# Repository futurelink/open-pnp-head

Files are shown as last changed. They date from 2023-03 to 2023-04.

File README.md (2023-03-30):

Versatile 4-nozzle PNP head controller
---

This controller was designed to be built into most of DIY pick-n-place machine heads.

### Features:
 - STM32F103C8T6 cheap MCU running on 72MHz
 - RS-485 control port
 - 4 rotary steppers running low-power STSPIN220 drivers
 - 2 up-down steppers running Pololu modules on your taste
 - 4 vacuum sensors to control part presence and place success
 - 4 isolated end-stop ports for home position identification
 - 4 isolated AO3400 MOSFET-driven ports to connect valves, solenoids etc.
 - head top light either WS2812 or LED-strip (5 or 12v)
 - Small size 80x65mm
 - No parts smaller than 0603 so can be hand-built.

### Board render:

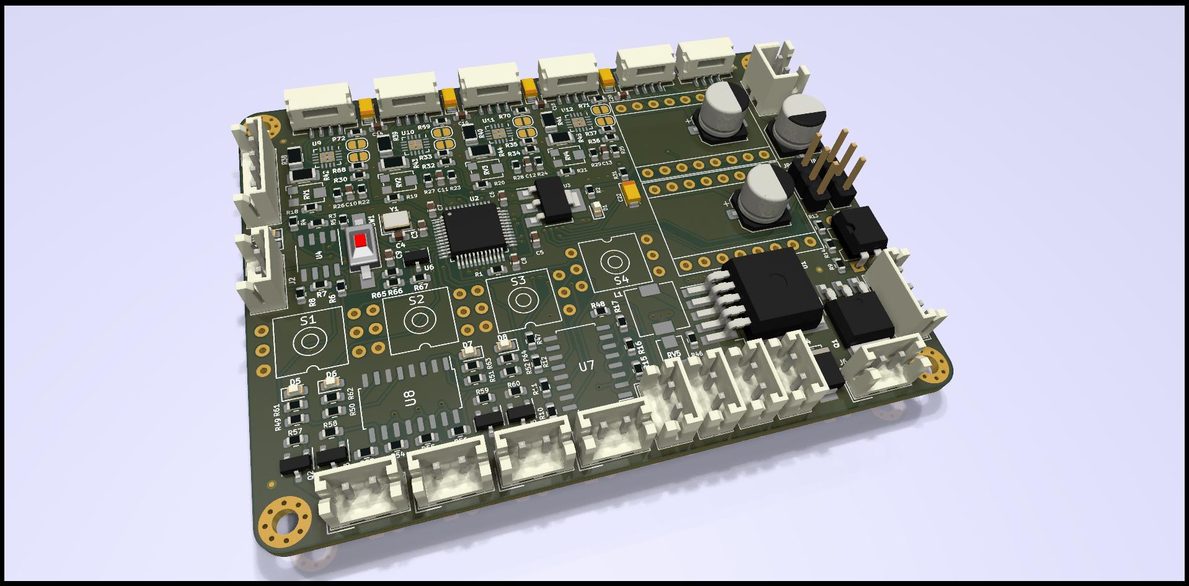
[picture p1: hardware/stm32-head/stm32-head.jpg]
render


### Disclaimer

This project is still in development, and it's not production ready.

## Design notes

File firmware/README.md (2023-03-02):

Modular CNC controller
---

This project is based on GRBL source code, deeply refactored, rewritten in C++
to make the code easier to understand and support.

Target platform to run this firmware is STM32F103C8T6, although it can be easily ported
to any other 32-bit MCU. Binary size with all available options switched on is about
76Kb.

### Supported hardware features

Mostly all features were derived from GRBL, some of them were added.

- Spindle (including PWM controlled)
- Coolant (Flood and Mist outputs)
- Limit switches (X, Y and Z)
- Probe
- Control inputs (Cycle start, Feed Hold, Reset and Safety door)
- Relay control 5 channels (turn on commands M100-M104, turn off - M110-M114)

### Running this firmware

Shortly - it can be run on a 'Blue Pill', USB is configured as Virtual COM port,
hence it's used to control and send G-Code. Typical speed is 115200.

Another option is to use controller designed for this firmware and it worth it because it has:

- opto-couplers in input and output lines (excluding control port and stepper drivers)
- RS-485 interface to control additional hardware
- 2 types of USB connectors (USB-B and JST embedding into one case with PC)
- 4 channels with MOSFETs to control relays (valves, solenoids) and separate (max. 24V) relay power input
- 1 channel with the same MOSFET but switchable power supply to connect work zone light
- spindle control 0-10V

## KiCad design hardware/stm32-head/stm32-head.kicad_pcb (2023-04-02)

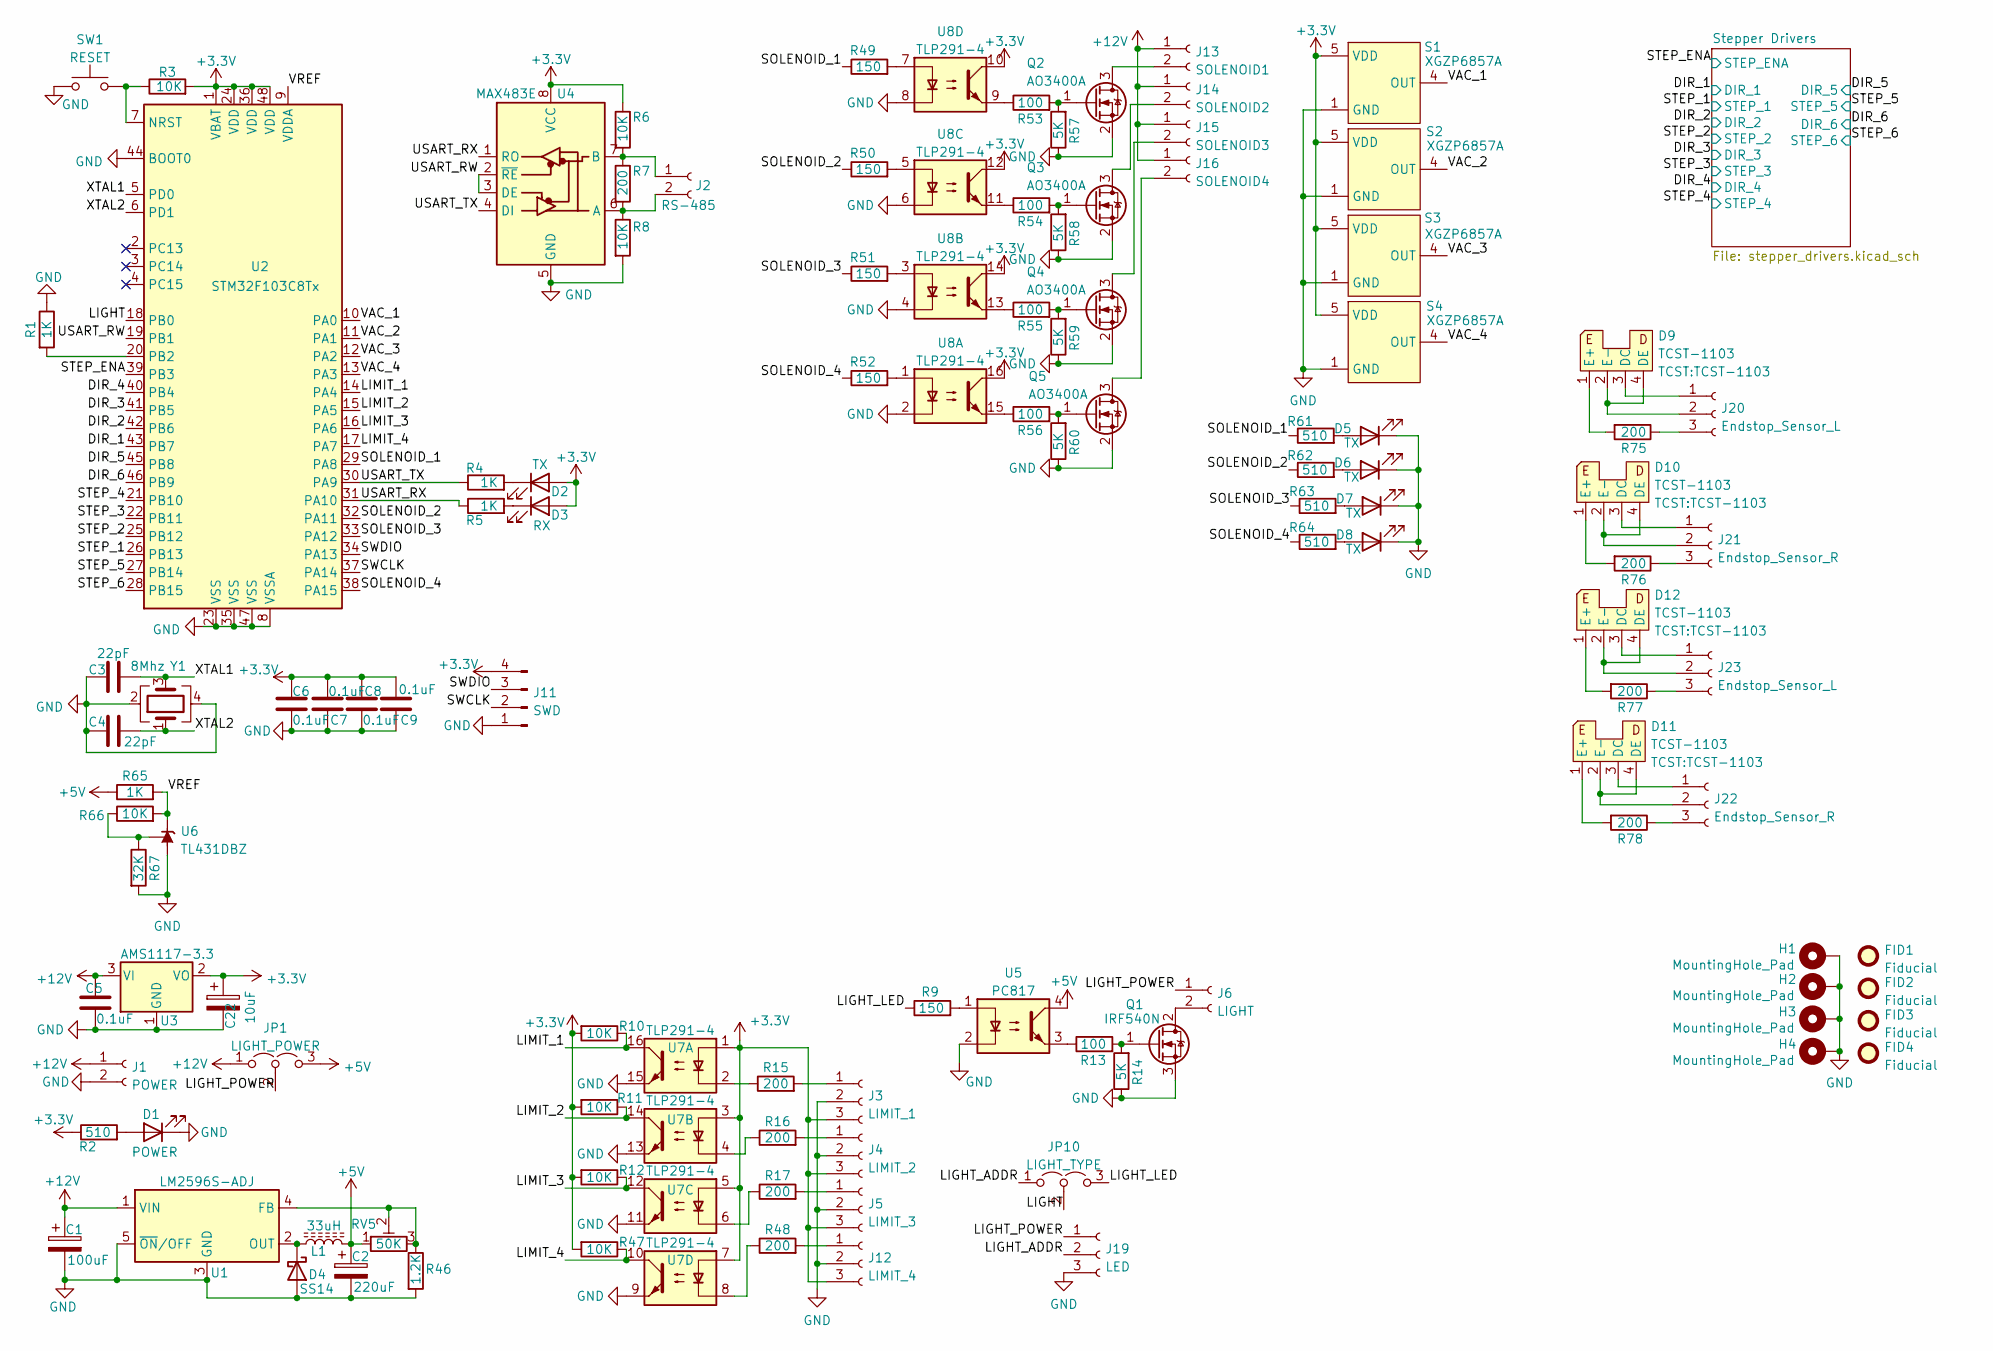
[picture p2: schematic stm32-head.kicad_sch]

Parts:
C1: 100uF; CP_Elec_6.3x5.9
C2: 220uF; CP_EIA-7343-31_Kemet-D
C3, C4: 22pF; C_0603_1608Metric
C5, C6, C7, C8, C9: 0.1uF; C_0603_1608Metric
C22: 10uF; CP_EIA-3216-12_Kemet-S
D1: POWER; LED_0603_1608Metric
D2, D5, D6, D7, D8: TX; LED_0603_1608Metric
D3: RX; LED_0603_1608Metric
D4: SS14; D_SMB
D9, D10, D11, D12: TCST-1103
FID1, FID2, FID3, FID4: Fiducial; Fiducial_0.5mm_Mask1mm
H1, H2, H3, H4: MountingHole_Pad; MountingHole_2.5mm_Pad_Via
J1: POWER; JST_XH_B2B-XH-A_1x02_P2.50mm_Vertical
J2: RS-485; JST_EH_B2B-EH-A_1x02_P2.50mm_Vertical
J3: LIMIT_1; JST_GH_BM03B-GHS-TBT_1x03-1MP_P1.25mm_Vertical
J4: LIMIT_2; JST_GH_BM03B-GHS-TBT_1x03-1MP_P1.25mm_Vertical
J5: LIMIT_3; JST_GH_BM03B-GHS-TBT_1x03-1MP_P1.25mm_Vertical
J6: LIGHT; JST_GH_BM02B-GHS-TBT_1x02-1MP_P1.25mm_Vertical
J11: SWD; JST_EH_B4B-EH-A_1x04_P2.50mm_Vertical
J12: LIMIT_4; JST_GH_BM03B-GHS-TBT_1x03-1MP_P1.25mm_Vertical
J13: SOLENOID1; JST_EH_B2B-EH-A_1x02_P2.50mm_Vertical
J14: SOLENOID2; JST_EH_B2B-EH-A_1x02_P2.50mm_Vertical
J15: SOLENOID3; JST_EH_B2B-EH-A_1x02_P2.50mm_Vertical
J16: SOLENOID4; JST_EH_B2B-EH-A_1x02_P2.50mm_Vertical
J19: LED; JST_EH_B3B-EH-A_1x03_P2.50mm_Vertical
J20, J23: Endstop_Sensor_L; JST_GH_SM03B-GHS-TB_1x03-1MP_P1.25mm_Horizontal
J21, J22: Endstop_Sensor_R; JST_GH_SM03B-GHS-TB_1x03-1MP_P1.25mm_Horizontal
JP1: LIGHT_POWER; PinHeader_1x03_P2.54mm_Vertical
JP10: LIGHT_TYPE; PinHeader_1x03_P2.54mm_Vertical
L1: 33uH; L_6.3x6.3_H3
Q1: IRF540N; TO-252-3_TabPin2
Q2, Q3, Q4, Q5: AO3400A; SOT-23
R1, R4, R5, R65: 1K; R_0603_1608Metric
R2, R61, R62, R63, R64: 510; R_0603_1608Metric
R3, R6, R8, R10, R11, R12, R47, R66: 10K; R_0603_1608Metric
R7, R15, R16, R17, R48, R75, R76, R77, R78: 200; R_0603_1608Metric
R9, R49, R50, R51, R52: 150; R_0603_1608Metric
R13, R53, R54, R55, R56: 100; R_0603_1608Metric
R14, R57, R58, R59, R60: 5K; R_0603_1608Metric
R46: 1.2K; R_0603_1608Metric
R67: 32K; R_0603_1608Metric
RV5: 50K; Potentiometer_Bourns_TC33X_Vertical
S1, S2, S3, S4: XGZP6857A; XGZP_Sensor_THT
SW1: RESET; SW_SPST_FSMSM
U1: LM2596S-ADJ; TO-263-5_TabPin3
U2: STM32F103C8Tx; LQFP-48_7x7mm_P0.5mm
U3: AMS1117-3.3; SOT-223-3_TabPin2
U4: MAX483E; SO-8_3.9x4.9mm_P1.27mm
U5: PC817; DIP-4_W7.62mm
U6: TL431DBZ; SOT-23
U7, U8: TLP291-4; SOIC-16_4.55x10.3mm_P1.27mm
Y1: 8Mhz; Crystal_SMD_3225-4Pin_3.2x2.5mm

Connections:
+3.3V: C6.2, C7.2, C8.2, C9.2, C22.1, D2.2 (A), D3.2 (A), J3.3, J4.3, J5.3, J11.4, J12.3, R2.1, R3.2, R6.1, R10.2, R11.2, R12.2, R47.2, S1.5 (VDD), S2.5 (VDD), S3.5 (VDD), S4.5 (VDD), U2.1 (VBAT), U2.24 (VDD), U2.36 (VDD), U2.48 (VDD), U3.2 (VO), U4.8 (VCC), U7.1, U7.3, U7.5, U7.7, U8.10, U8.12, U8.14, U8.16; also elsewhere on the board
+5V: C2.1, JP1.3 (B), L1.2, R65.1, RV5.1, U5.4; also elsewhere on the board
+12V: C1.1, C5.2, J1.1, J13.1, J14.1, J15.1, J16.1, JP1.1 (A), U1.1 (VIN), U3.3 (VI); also elsewhere on the board
/DIR_1: U2.43 (PB7); also elsewhere on the board
/DIR_2: U2.42 (PB6); also elsewhere on the board
/DIR_3: U2.41 (PB5); also elsewhere on the board
/DIR_4: U2.40 (PB4); also elsewhere on the board
/DIR_5: U2.45 (PB8); also elsewhere on the board
/DIR_6: U2.46 (PB9); also elsewhere on the board
/LIGHT: JP10.2 (C), U2.18 (PB0)
/LIGHT_ADDR: J19.2, JP10.1 (A)
/LIGHT_LED: JP10.3 (B), R9.1
/LIGHT_POWER: J6.1, J19.1, JP1.2 (C)
/LIMIT_1: R10.1, U2.14 (PA4), U7.16
/LIMIT_2: R11.1, U2.15 (PA5), U7.14
/LIMIT_3: R12.1, U2.16 (PA6), U7.12
/LIMIT_4: R47.1, U2.17 (PA7), U7.10
/SOLENOID_1: R49.1, R61.1, U2.29 (PA8)
/SOLENOID_2: R50.1, R62.1, U2.32 (PA11)
/SOLENOID_3: R51.1, R63.1, U2.33 (PA12)
/SOLENOID_4: R52.1, R64.1, U2.38 (PA15)
/STEP_1: U2.26 (PB13); also elsewhere on the board
/STEP_2: U2.25 (PB12); also elsewhere on the board
/STEP_3: U2.22 (PB11); also elsewhere on the board
/STEP_4: U2.21 (PB10); also elsewhere on the board
/STEP_5: U2.27 (PB14); also elsewhere on the board
/STEP_6: U2.28 (PB15); also elsewhere on the board
/STEP_ENA: U2.39 (PB3); also elsewhere on the board
/SWCLK: J11.2, U2.37 (PA14)
/SWDIO: J11.3, U2.34 (PA13)
/USART_RW: U2.19 (PB1), U4.2 (~RE), U4.3 (DE)
/USART_RX: R5.1, U2.31 (PA10), U4.1 (RO)
/USART_TX: R4.1, U2.30 (PA9), U4.4 (DI)
/VAC_1: S1.4 (OUT), U2.10 (PA0)
/VAC_2: S2.4 (OUT), U2.11 (PA1)
/VAC_3: S3.4 (OUT), U2.12 (PA2)
/VAC_4: S4.4 (OUT), U2.13 (PA3)
/VREF: R65.2, R66.2, U2.9 (VDDA), U6.1 (K)
/XTAL1: C3.2, U2.5 (PD0), Y1.3
/XTAL2: C4.2, U2.6 (PD1), Y1.1
GND: C1.2, C2.2, C3.1, C4.1, C5.1, C6.1, C7.1, C8.1, C9.1, C22.2, D1.1 (K), D4.2 (A), D5.1 (K), D6.1 (K), D7.1 (K), D8.1 (K), H1.1, H2.1, H3.1, H4.1, J1.2, J3.2, J4.2, J5.2, J11.1, J12.2, J19.3, Q1.3 (S), Q2.2 (S), Q3.2 (S), Q4.2 (S), Q5.2 (S), R1.1, R8.2, R14.1, R46.2, R57.1, R58.1, R59.1, R60.1, R67.2, S1.1 (GND), S2.1 (GND), S3.1 (GND), S4.1 (GND), SW1.1, U1.3 (GND), U1.5 (~ON/OFF), U2.8 (VSSA), U2.23 (VSS), U2.35 (VSS), U2.44 (BOOT0), U2.47 (VSS), U3.1 (GND), U4.5 (GND), U5.2, U6.3 (A), U7.9, U7.11, U7.13, U7.15, U8.2, U8.4, U8.6, U8.8, Y1.2, Y1.4; also elsewhere on the board
unnamed: D1.2 (A), R2.2
unnamed: D2.1 (K), R4.2
unnamed: D3.1 (K), R5.2
unnamed: D4.1 (K), L1.1, U1.2 (OUT)
unnamed: D5.2 (A), R61.2
unnamed: D6.2 (A), R62.2
unnamed: D7.2 (A), R63.2
unnamed: D8.2 (A), R64.2
unnamed: D9.1 (E+), R75.2
unnamed: D9.2 (E-), D9.4 (DE), J20.2
unnamed: D9.3 (DC), J20.1
unnamed: D10.1 (E+), R76.2
unnamed: D10.2 (E-), D10.4 (DE), J21.2
unnamed: D10.3 (DC), J21.1
unnamed: D11.1 (E+), R78.2
unnamed: D11.2 (E-), D11.4 (DE), J22.2
unnamed: D11.3 (DC), J22.1
unnamed: D12.1 (E+), R77.2
unnamed: D12.2 (E-), D12.4 (DE), J23.2
unnamed: D12.3 (DC), J23.1
unnamed: J2.1, R6.2, R7.1, U4.7 (B)
unnamed: J2.2, R7.2, R8.1, U4.6 (A)
unnamed: J3.1, R15.2
unnamed: J4.1, R16.2
unnamed: J5.1, R17.2
unnamed: J6.2, Q1.2 (D)
unnamed: J12.1, R48.2
unnamed: J13.2, Q2.3 (D)
unnamed: J14.2, Q3.3 (D)
unnamed: J15.2, Q4.3 (D)
unnamed: J16.2, Q5.3 (D)
unnamed: J20.3, R75.1
unnamed: J21.3, R76.1
unnamed: J22.3, R78.1
unnamed: J23.3, R77.1
unnamed: Q1.1 (G), R13.2, R14.2
unnamed: Q2.1 (G), R53.2, R57.2
unnamed: Q3.1 (G), R54.2, R58.2
unnamed: Q4.1 (G), R55.2, R59.2
unnamed: Q5.1 (G), R56.2, R60.2
unnamed: R1.2, U2.20 (PB2)
unnamed: R3.1, SW1.2, U2.7 (NRST)
unnamed: R9.2, U5.1
unnamed: R13.1, U5.3
unnamed: R15.1, U7.2
unnamed: R16.1, U7.4
unnamed: R17.1, U7.6
unnamed: R46.1, RV5.2, RV5.3, U1.4 (FB)
unnamed: R48.1, U7.8
unnamed: R49.2, U8.7
unnamed: R50.2, U8.5
unnamed: R51.2, U8.3
unnamed: R52.2, U8.1
unnamed: R53.1, U8.9
unnamed: R54.1, U8.11
unnamed: R55.1, U8.13
unnamed: R56.1, U8.15
unnamed: R66.1, R67.1, U6.2 (REF)

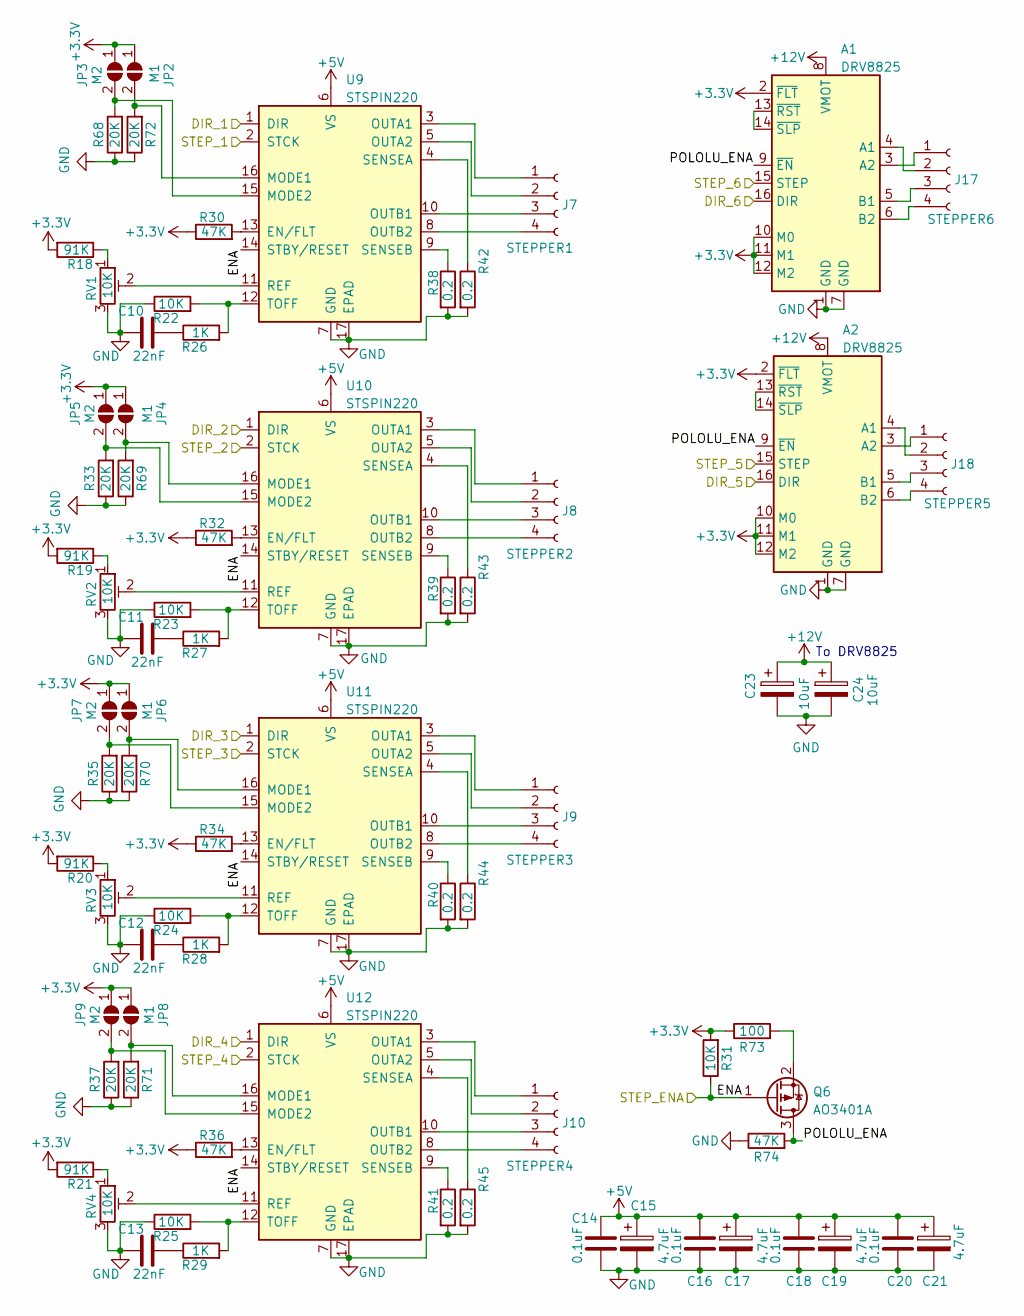
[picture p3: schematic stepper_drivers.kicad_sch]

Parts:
A1, A2: DRV8825; Pololu_Breakout-16_15.2x20.3mm
C10, C11, C12, C13: 22nF; C_0603_1608Metric
C14, C16, C18, C20: 0.1uF; C_0603_1608Metric
C15, C17, C19, C21: 4.7uF; CP_EIA-3216-10_Kemet-I
C23, C24: 10uF; CP_Elec_6.3x5.9
J7: STEPPER1; JST_GH_SM04B-GHS-TB_1x04-1MP_P1.25mm_Horizontal
J8: STEPPER2; JST_GH_SM04B-GHS-TB_1x04-1MP_P1.25mm_Horizontal
J9: STEPPER3; JST_GH_SM04B-GHS-TB_1x04-1MP_P1.25mm_Horizontal
J10: STEPPER4; JST_GH_SM04B-GHS-TB_1x04-1MP_P1.25mm_Horizontal
J17: STEPPER6; JST_GH_SM04B-GHS-TB_1x04-1MP_P1.25mm_Horizontal
J18: STEPPER5; JST_GH_SM04B-GHS-TB_1x04-1MP_P1.25mm_Horizontal
JP2, JP4, JP6, JP8: M1; SolderJumper-2_P1.3mm_Open_RoundedPad1.0x1.5mm
JP3, JP5, JP7, JP9: M2; SolderJumper-2_P1.3mm_Open_RoundedPad1.0x1.5mm
Q6: AO3401A; SOT-23
R18, R19, R20, R21: 91K; R_0603_1608Metric
R22, R23, R24, R25, R31: 10K; R_0603_1608Metric
R26, R27, R28, R29: 1K; R_0603_1608Metric
R30, R32, R34, R36, R74: 47K; R_0603_1608Metric
R33, R35, R37, R68, R69, R70, R71, R72: 20K; R_0603_1608Metric
R38, R39, R40, R41, R42, R43, R44, R45: 0.2; R_1206_3216Metric
R73: 100; R_0603_1608Metric
RV1, RV2, RV3, RV4: 10K; Potentiometer_Bourns_TC33X_Vertical
U9, U10, U11, U12: STSPIN220; VQFN-16-1EP_3x3mm_P0.5mm_EP1.8x1.8mm

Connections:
+3.3V: A1.2 (~FLT), A1.10 (M0), A1.11 (M1), A1.12 (M2), A2.2 (~FLT), A2.10 (M0), A2.11 (M1), A2.12 (M2), JP2.1 (A), JP3.1 (A), JP4.1 (A), JP5.1 (A), JP6.1 (A), JP7.1 (A), JP8.1 (A), JP9.1 (A), R18.2, R19.2, R20.2, R21.2, R30.1, R31.2, R32.1, R34.1, R36.1, R73.1; also elsewhere on the board
+5V: C14.1, C15.1, C16.1, C17.1, C18.1, C19.1, C20.1, C21.1, U9.6 (VS), U10.6 (VS), U11.6 (VS), U12.6 (VS); also elsewhere on the board
+12V: A1.8 (VMOT), A2.8 (VMOT), C23.1, C24.1; also elsewhere on the board
/DIR_1: U9.1 (DIR); also elsewhere on the board
/DIR_2: U10.1 (DIR); also elsewhere on the board
/DIR_3: U11.1 (DIR); also elsewhere on the board
/DIR_4: U12.1 (DIR); also elsewhere on the board
/DIR_5: A2.16 (DIR); also elsewhere on the board
/DIR_6: A1.16 (DIR); also elsewhere on the board
/STEP_1: U9.2 (STCK); also elsewhere on the board
/STEP_2: U10.2 (STCK); also elsewhere on the board
/STEP_3: U11.2 (STCK); also elsewhere on the board
/STEP_4: U12.2 (STCK); also elsewhere on the board
/STEP_5: A2.15 (STEP); also elsewhere on the board
/STEP_6: A1.15 (STEP); also elsewhere on the board
/STEP_ENA: Q6.1 (G), R31.1, U9.14 (STBY/RESET), U10.14 (STBY/RESET), U11.14 (STBY/RESET), U12.14 (STBY/RESET); also elsewhere on the board
/Stepper Drivers/POLOLU_ENA: A1.9 (~EN), A2.9 (~EN), Q6.3 (D), R74.2
GND: A1.1 (GND), A1.7 (GND), A2.1 (GND), A2.7 (GND), C10.1, C11.1, C12.1, C13.1, C14.2, C15.2, C16.2, C17.2, C18.2, C19.2, C20.2, C21.2, C23.2, C24.2, R22.1, R23.1, R24.1, R25.1, R33.1, R35.1, R37.1, R38.2, R39.2, R40.2, R41.2, R42.2, R43.2, R44.2, R45.2, R68.1, R69.1, R70.1, R71.1, R72.1, R74.1, RV1.3, RV2.3, RV3.3, RV4.3, U9.7 (GND), U9.17 (EPAD), U10.7 (GND), U10.17 (EPAD), U11.7 (GND), U11.17 (EPAD), U12.7 (GND), U12.17 (EPAD); also elsewhere on the board
unnamed: A1.3 (A2), J17.1
unnamed: A1.4 (A1), J17.2
unnamed: A1.5 (B1), J17.3
unnamed: A1.6 (B2), J17.4
unnamed: A1.13 (~RST), A1.14 (~SLP)
unnamed: A2.3 (A2), J18.1
unnamed: A2.4 (A1), J18.2
unnamed: A2.5 (B1), J18.3
unnamed: A2.6 (B2), J18.4
unnamed: A2.13 (~RST), A2.14 (~SLP)
unnamed: C10.2, R26.1
unnamed: C11.2, R27.1
unnamed: C12.2, R28.1
unnamed: C13.2, R29.1
unnamed: J7.1, U9.3 (OUTA1)
unnamed: J7.2, U9.5 (OUTA2)
unnamed: J7.3, U9.10 (OUTB1)
unnamed: J7.4, U9.8 (OUTB2)
unnamed: J8.1, U10.3 (OUTA1)
unnamed: J8.2, U10.5 (OUTA2)
unnamed: J8.3, U10.10 (OUTB1)
unnamed: J8.4, U10.8 (OUTB2)
unnamed: J9.1, U11.3 (OUTA1)
unnamed: J9.2, U11.5 (OUTA2)
unnamed: J9.3, U11.10 (OUTB1)
unnamed: J9.4, U11.8 (OUTB2)
unnamed: J10.1, U12.3 (OUTA1)
unnamed: J10.2, U12.5 (OUTA2)
unnamed: J10.3, U12.10 (OUTB1)
unnamed: J10.4, U12.8 (OUTB2)
unnamed: JP2.2 (B), R72.2, U9.16 (MODE1)
unnamed: JP3.2 (B), R68.2, U9.15 (MODE2)
unnamed: JP4.2 (B), R69.2, U10.16 (MODE1)
unnamed: JP5.2 (B), R33.2, U10.15 (MODE2)
unnamed: JP6.2 (B), R70.2, U11.16 (MODE1)
unnamed: JP7.2 (B), R35.2, U11.15 (MODE2)
unnamed: JP8.2 (B), R71.2, U12.16 (MODE1)
unnamed: JP9.2 (B), R37.2, U12.15 (MODE2)
unnamed: Q6.2 (S), R73.2
unnamed: R18.1, RV1.1
unnamed: R19.1, RV2.1
unnamed: R20.1, RV3.1
unnamed: R21.1, RV4.1
unnamed: R22.2, R26.2, U9.12 (TOFF)
unnamed: R23.2, R27.2, U10.12 (TOFF)
unnamed: R24.2, R28.2, U11.12 (TOFF)
unnamed: R25.2, R29.2, U12.12 (TOFF)
unnamed: R30.2, U9.13 (EN/FLT)
unnamed: R32.2, U10.13 (EN/FLT)
unnamed: R34.2, U11.13 (EN/FLT)
unnamed: R36.2, U12.13 (EN/FLT)
unnamed: R38.1, U9.9 (SENSEB)
unnamed: R39.1, U10.9 (SENSEB)
unnamed: R40.1, U11.9 (SENSEB)
unnamed: R41.1, U12.9 (SENSEB)
unnamed: R42.1, U9.4 (SENSEA)
unnamed: R43.1, U10.4 (SENSEA)
unnamed: R44.1, U11.4 (SENSEA)
unnamed: R45.1, U12.4 (SENSEA)
unnamed: RV1.2, U9.11 (REF)
unnamed: RV2.2, U10.11 (REF)
unnamed: RV3.2, U11.11 (REF)
unnamed: RV4.2, U12.11 (REF)

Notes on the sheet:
To DRV8825

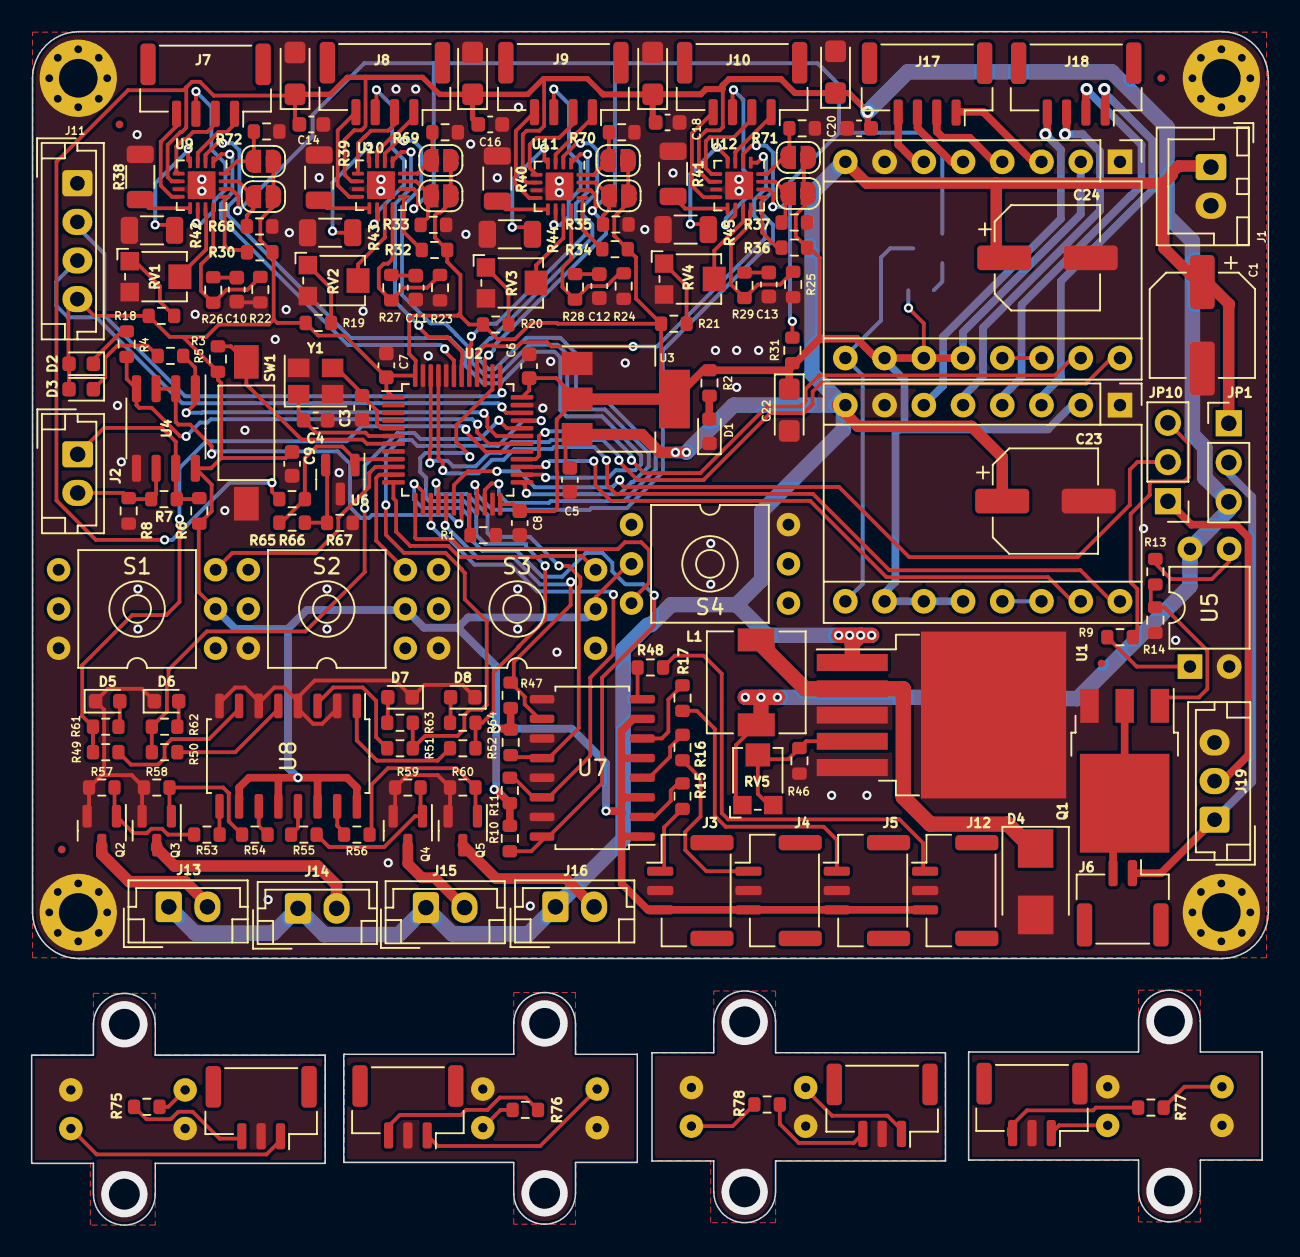
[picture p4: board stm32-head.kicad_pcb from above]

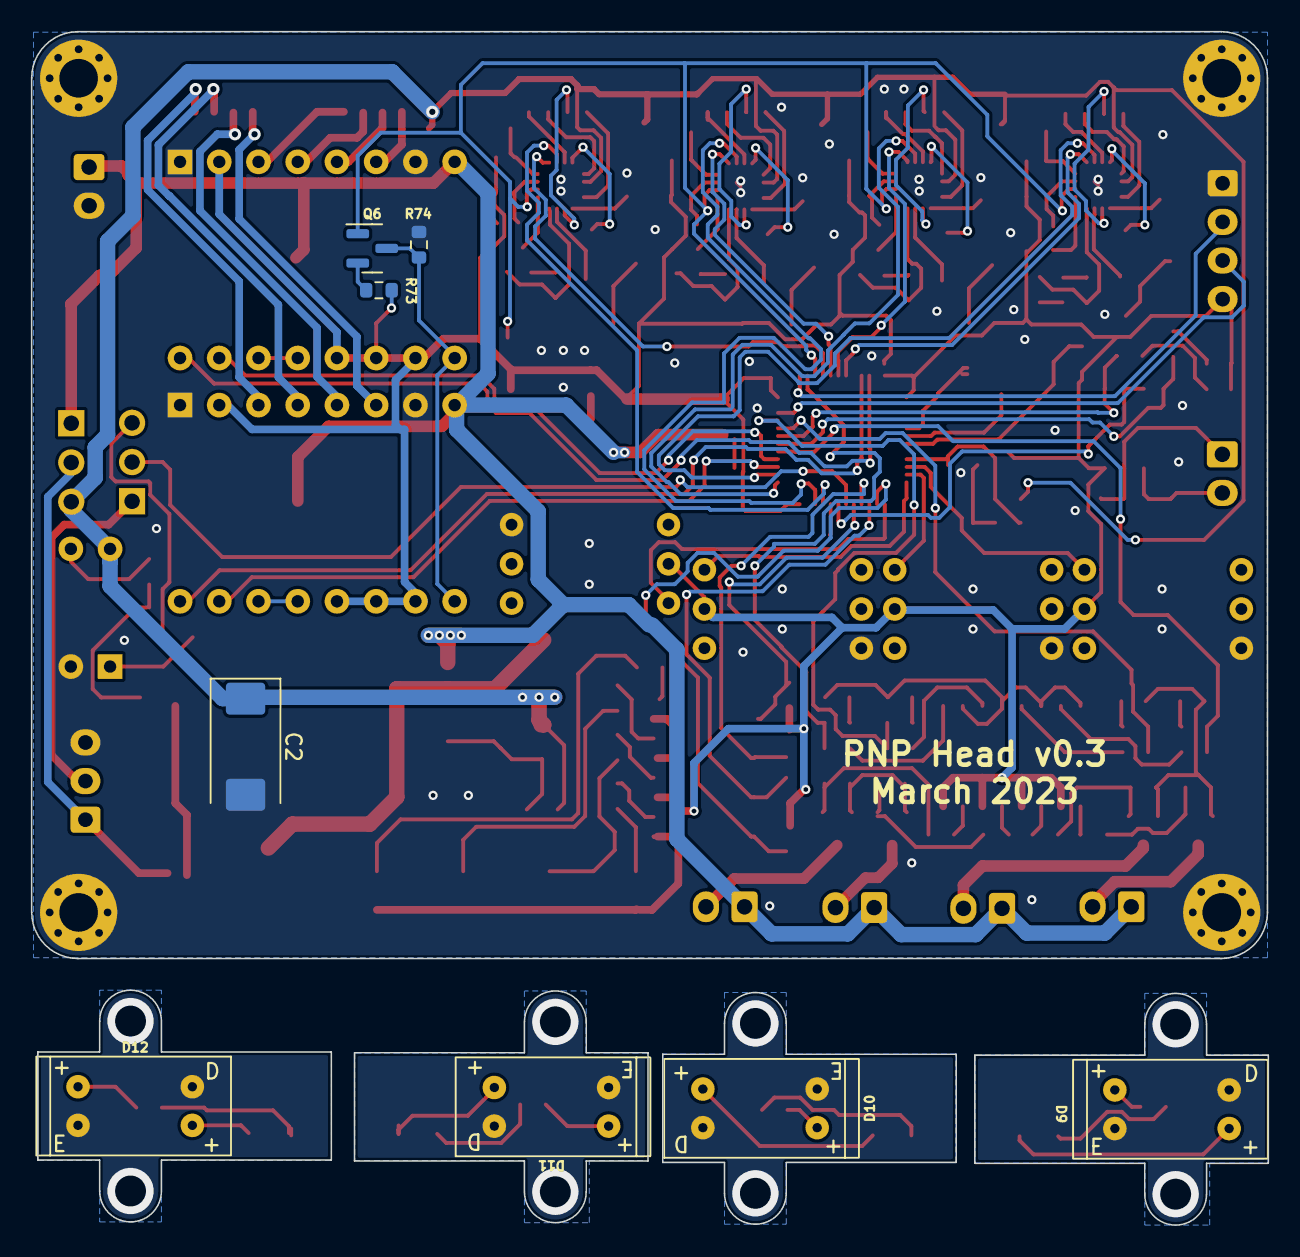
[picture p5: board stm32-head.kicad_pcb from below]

Board: 2 copper layers, 80.0 x 60.0 mm, 187 parts (8 on the bottom side), 163 nets.

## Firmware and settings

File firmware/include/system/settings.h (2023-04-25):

/*
  settings.h
  Part of open-pnp-head

  Copyright (c) 2022 Denis Pavlov

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
  You should have received a copy of the GNU General Public License
  along with open-pnp-head.  If not, see <http://www.gnu.org/licenses/>.
*/

#ifndef SETTINGS_H
#define SETTINGS_H

#include "config.h"

#include <cstdint>

#define SETTINGS_VERSION 1

class Settings {
private:
    float       steps_per_degree;

    // Linear belt-driven head settings
    uint16_t    steps_per_mm;

#ifdef ROCKER_HEAD
    // Rocker-head settings
    float       arm_length;
    float       arm_center_offset;
    float       arm_roller_radius;

    // Internal variables
    float       arm_max_travel;
    float       arm_segment_length;
    float       step_increment[STEP_APPROX_SEGMENTS_N];
#endif

public:
    Settings();

    bool load();

    float get_steps_per_degree(uint8_t axis) const;
    uint16_t get_steps_per_mm(uint8_t axis) const;

    float get_acceleration(uint8_t axis) const;
    float get_speed(uint8_t axis) const;

    void convert_rotary_steps_to_degrees(float *position, const int32_t *steps, uint8_t n_axis) const;
    void convert_linear_steps_to_mm(float *position, const int32_t *steps, uint8_t n_axis) const;
    float convert_linear_steps_to_mm(int32_t steps) const;

    float get_linear_max_travel();

#ifdef ROCKER_HEAD
    void prepare_rocker_head_curve();
    float get_rocker_axis_position(int32_t position_steps) const;
    float get_rocker_axis_steps(float position, float destination) const;
#endif


};

inline float Settings::get_steps_per_degree(uint8_t axis) const { return steps_per_degree; }
inline uint16_t Settings::get_steps_per_mm(uint8_t axis) const { return steps_per_mm; }

#endif //SETTINGS_H

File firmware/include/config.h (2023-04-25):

/*
  config.h - main configuration
  Part of open-pnp-head

  Copyright (c) 2022 Denis Pavlov

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
  You should have received a copy of the GNU General Public License
  along with open-pnp-head.  If not, see <http://www.gnu.org/licenses/>.
*/

#include <cstdint>

#ifndef CONFIG_H
#define CONFIG_H

// Enables ModBus mode
#define MODBUS

#define BAUD_RATE           115200

#define GREETING_STRING     "PNP Head / v0.1\n"
#define LINE_MAX_LENGTH     80

// Turns on rocker head mode.
// Comment out to switch to linear movement mode
// ---------------------------------------------
#define ROCKER_HEAD

#define ROTARY_AXIS_N       4                       // Number of rotary axes i.e. nozzles
#define LINEAR_AXIS_N       (ROTARY_AXIS_N / 2)     // Number of linear/rocker axes
#define AXIS_N              (ROTARY_AXIS_N + LINEAR_AXIS_N)

// Axis direction inverted
#define AXIS_DIR_INVERT  ((1 << 0) | (1 << 1) | (2 << 1) | (3 << 1)) // All rotary axes

// Axis speed/acceleration settings
// --------------------------------
#define ROTARY_AXIS_ACCEL       25000               // deg/s^2
#define ROTARY_AXIS_SPEED       2500                // deg/s
#define ROTARY_STEP_PER_DEGREE  (200.0 * 16 / 360)  // steps/deg, 1/16 micro-step

// Vacuum sensors settings and minimum values
// ------------------------------------------
#define VAC_SENSORS_N                   4
#define VAC_SENSOR_1_MIN_PRESSURE       (-100) // kPa
#define VAC_SENSOR_2_MIN_PRESSURE       (-100) // kPa
#define VAC_SENSOR_3_MIN_PRESSURE       (-100) // kPa
#define VAC_SENSOR_4_MIN_PRESSURE       (-100) // kPa

// Number of relay outputs
// -----------------------
#define RELAY_N                         4

// Vacuum values with components sucked to nozzle
// ----------------------------------------------
#define VAC_SENSOR_1_LOCKED_PRESSURE    (-0.01) // kPa
#define VAC_SENSOR_2_LOCKED_PRESSURE    (-5) // kPa
#define VAC_SENSOR_3_LOCKED_PRESSURE    (-5) // kPa
#define VAC_SENSOR_4_LOCKED_PRESSURE    (-5) // kPa

#define STEPPER_ENABLE_INVERT
#define ACCELERATION_TICKS_PER_SECOND   50
#define STEP_PULSE_MS                   2

// Time in milliseconds to wait while pressure normalizes before measuring
// -----------------------------------------------------------------------
#define PICK_WAIT_TIME                  100  // when picking
#define PLACE_WAIT_TIME                 150  // when placing

// Rocker head settings
// --------------------
#ifdef ROCKER_HEAD
#define LINEAR_AXIS_ACCEL               4000                // mm/s^2
#define LINEAR_AXIS_SPEED               4000                // mm/s
#define STEP_PER_ROTATION               12800
#define STEP_APPROX_SEGMENTS_N          20
#define ARM_LENGTH                      31    // mm
#define ARM_CENTER_OFFSET               7       // mm
#define ARM_ROLLER_RADIUS               5       // mm
#else
#define LINEAR_AXIS_ACCEL               4000                // mm/s^2
#define LINEAR_AXIS_SPEED               4000                // mm/s
#define LINEAR_AXIS_MAX_TRAVEL          50.0F               // mm
#define LINEAR_STEP_PER_MM              160.0F              // steps/mm
#endif

// Addressable LED light settings
// ------------------------------
#define WS8212LED                               // Turns on addressable LEDs support
#define WS8212LED_N                     16      // LEDs number

#endif // CONFIG_H

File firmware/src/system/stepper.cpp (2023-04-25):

/*
  stepper.cpp - step motor control routines
  Part of open-pnp-head

  Copyright (c) 2022 Denis Pavlov

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
  You should have received a copy of the GNU General Public License
  along with open-pnp-head.  If not, see <http://www.gnu.org/licenses/>.
*/

#include <cmath>
#include <cstring>

#include "config.h"
#include "system/stepper.h"
#include "system/macros.h"
#include "stm32/stm32_routines.h"

Steppers::Steppers(Settings *settings, State *state, Callbacks *callbacks) {
    this->settings = settings;
    this->state = state;
    this->callbacks = callbacks;
    this->step_port_invert_mask = 0xffff;
    this->dir_port_invert_mask = axis_to_port_direction_bits(AXIS_DIR_INVERT);

    // Initialize structs with zeroes
    memset(&profile, 0, sizeof(profile_prep_t));
    memset(&st, 0, sizeof(stepper_t));

    this->planned_block = nullptr;
    this->segment_buffer_tail = 0;
    this->segment_buffer_head = 0;
    this->segment_next_head = 1;
    this->busy = false;

    this->segment_dt = 0;
    this->units_remaining = 0;
}

void Steppers::init() {
    stm32_stepper_init();
    go_idle();
    stm32_steppers_set(dir_port_invert_mask, step_port_invert_mask);
}

void Steppers::pulse_start() {
    if (!stm32_steppers_pulse_start(busy, st.dir_out_bits, st.step_out_bits)) return;

    busy = true;

    // If there is no step segment, attempt to pop one from the stepper buffer
    if (st.exec_segment == nullptr) {
        if (segment_buffer_head != segment_buffer_tail) { // Anything in the buffer? If so, load and initialize next step segment.
            st.exec_segment = &segment_buffer[segment_buffer_tail]; // Initialize new step segment and load number of steps to execute

            // Initialize step segment timing per step and load number of steps to execute.
            stm32_steppers_set_timer(st.exec_segment->cycles_per_tick);
            st.step_count = st.exec_segment->n_step;

            // If the new segment starts a new planner block, initialize stepper variables and counters.
            // NOTE: When the segment data index changes, this indicates a new planner block.
            if (st.exec_block_index != st.exec_segment->st_block_index) {
                st.exec_block_index = st.exec_segment->st_block_index;
                st.exec_block = &st_block_buffer[st.exec_block_index];

                // Initialize Bresenham line and distance counters
                for (uint32_t &counter : st.counters) counter = st.exec_block->step_event_count >> 1;
            }

            st.dir_out_bits = st.exec_block->dir_port_bits ^ dir_port_invert_mask;

            // With AMASS enabled, adjust Bresenham axis increment counters according to AMASS level
            for (uint8_t idx = 0; idx < (uint8_t) AXIS_N; idx++) {
                st.steps[idx] = st.exec_block->steps[idx] >> st.exec_segment->amass_level;
            }
        } else {
            go_idle(); // Segment buffer empty. Shutdown.
            state->set_state(state->get_state() | STATE_CYCLE_STOP);  // Flag for cycle end, keep cycle flag
            return;
        }
    }

    st.step_out_bits = 0; // Reset step out bits.

    // Execute step displacement profile by Bresenham line algorithm
    // -------------------------------------------------------------
    for (uint8_t idx = 0; idx < (uint8_t) AXIS_N; idx++) {
        st.counters[idx] += st.steps[idx];
        if (st.counters[idx] > st.exec_block->step_event_count) {
            st.step_out_bits |= step_pin_mask[idx];
            st.counters[idx] -= st.exec_block->step_event_count;
            if ((st.dir_out_bits ^ dir_port_invert_mask) & direction_pin_mask[idx])
                state->decrement_position(idx);
            else
                state->increment_position(idx);
        }
    }

    st.step_count--; // Decrement step events count
    if (st.step_count == 0) {
        st.exec_segment = nullptr; // Segment is complete. Discard current segment and advance segment indexing.

        uint8_t segment_tail_next = segment_buffer_tail + 1;
        segment_buffer_tail = (segment_tail_next == SEGMENT_BUFFER_SIZE) ? 0 : segment_tail_next;
    }

    st.step_out_bits ^= step_port_invert_mask;  // Apply step port invert mask
    busy = false;
}

void Steppers::pulse_end() const {
    stm32_steppers_pulse_end(step_port_invert_mask);
}

/**
 * Stepper state initialization
 */
void Steppers::wake_up() {
    stm32_steppers_enable();

    // Initialize stepper output bits to ensure first ISR call does not step.
    st.step_out_bits = step_port_invert_mask;

    // Set step pulse time. Ad-hoc computation from oscilloscope. Uses two's complement.
    st.step_pulse_time = STEP_PULSE_MS * TICKS_PER_MICROSECOND;

    stm32_steppers_wake_up(st.step_pulse_time, st.exec_segment->cycles_per_tick);
}

/**
 * Stepper shutdown
 */
void Steppers::go_idle() {
    stm32_steppers_go_idle();

    busy = false;
}

/**
 * Called by realtime status reporting to fetch the current speed being executed. This value
 * however is not exactly the current speed, but the speed computed in the last step segment
 * in the segment buffer. It will always be behind by up to the number of segment blocks (-1)
 * divided by the ACCELERATION TICKS PER SECOND in seconds.
 */
float Steppers::get_realtime_rate() const {
    return state->has_state(STATE_CYCLE_PICK | STATE_CYCLE_PLACE | STATE_CYCLE_ROTATE) ?
        profile.current_speed : 0.0f;
}

/**
 * Prepares buffer for stepper execution.
 * This method should be called as often as possible. Generally - from the main loop.
 */
void Steppers::prepare_buffer() {
    if (state->is_end_motion()) return;
    while (segment_buffer_tail != segment_next_head) {           // Check if we need to fill the buffer.
        if (!prepare_block()) return;                            // Bail out if there's no block to execute
        prepare_profile();
        prepare_segment(); // Initialize new segment
        if (check_end_motion()) {
            state->set_end_motion();
            return;
        }
    }
}
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

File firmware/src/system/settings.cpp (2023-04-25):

/*
  settings.cpp - settings management routines
  Part of open-pnp-head

  Copyright (c) 2022 Denis Pavlov

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
  You should have received a copy of the GNU General Public License
  along with open-pnp-head.  If not, see <http://www.gnu.org/licenses/>.
*/

#include "system/settings.h"

#include <cmath>

Settings::Settings() {

}

bool Settings::load() {
    steps_per_degree = ROTARY_STEP_PER_DEGREE; // 1/16 micro-stepping

#ifdef ROCKER_HEAD
    prepare_rocker_head_curve();
#else
    steps_per_mm = LINEAR_STEP_PER_MM;
#endif

    return true;
}

#ifdef ROCKER_HEAD
void Settings::prepare_rocker_head_curve() {
    arm_length = ARM_LENGTH;
    arm_center_offset = ARM_CENTER_OFFSET;
    arm_roller_radius = ARM_ROLLER_RADIUS;

    // Pre-calculate rocker-head curve approximation segments
    // ------------------------------------------------------
    auto steps_per_quarter = STEP_PER_ROTATION / 4;
    float degrees_per_step = 90.0f / (float) steps_per_quarter;
    arm_max_travel = arm_length - arm_center_offset + arm_roller_radius;
    arm_segment_length = arm_max_travel / STEP_APPROX_SEGMENTS_N;

    uint8_t segment = 0;
    uint16_t tmp_step_count = 0;
    float tmp_sum = 0;
    auto step = 0;
    auto step_radian = (float)(M_PI / 180 * degrees_per_step);
    while (step <= steps_per_quarter) {
        step++;
        tmp_sum += (sinf(step_radian * (float) step) - ((step == 0) ? 0.0f : sinf(step_radian * (float) (step - 1)))) * arm_max_travel;

        if ((tmp_sum >= arm_segment_length) || (step == steps_per_quarter)) {
            step_increment[segment] = arm_segment_length / (float) tmp_step_count;
            tmp_step_count = 0;
            tmp_sum -= (float) arm_segment_length;
            segment++;
        }
        tmp_step_count++;
    }
}

float Settings::get_rocker_axis_position(const int32_t position_steps) const {
    float position = 0;
    uint32_t abs_position_steps = abs(position_steps);

    // Calculate first incomplete segment steps
    // ...

    // Calculate full segments
    float steps = 0;
    uint8_t segment = 0;
    for (; segment < STEP_APPROX_SEGMENTS_N; segment++) {
        auto st_inc = arm_segment_length / step_increment[segment];
        if (steps + st_inc >= (float) abs_position_steps) break;
        position += arm_segment_length;
        steps += st_inc;
    }

    // Calculate remainder
    auto remain_steps = (float) abs_position_steps - steps;
    if (remain_steps > 0) position += remain_steps * step_increment[segment];

    return position * ((position_steps < 0) ? -1.0f : 1.0f);
}

float Settings::get_rocker_axis_steps(const float position, const float destination) const {
    if (position == destination) return 0;

    auto abs_position = fabsf(position);
    auto abs_destination = fabsf(destination);
    float steps = 0;

    // The main idea of this algorithm is to place finalizing segment at the end, so whatever
    // movement is being done the incomplete segment will always be the final thing to be processed.
    uint8_t dir = abs_position < abs_destination ? 0 : 1;
    auto start = (dir ? abs_destination : abs_position);
    auto end = (dir ? abs_position : abs_destination);
    auto segment = (uint8_t) floorf(start / arm_segment_length);        // First full segment
    auto last_segment = (uint8_t) floorf(end / arm_segment_length);    // Last full segment
    auto pos = abs_position;

    // Calculate first incomplete segment steps
    if ((float) segment != start / arm_segment_length) {
        auto dist = (arm_segment_length - start + ((float) segment * arm_segment_length));
        steps += dist / step_increment[segment];
        if (dir) pos -= dist; else pos += dist;
        segment++;
    }

    // Calculate internal full-segment steps
    while (segment < last_segment) {
        steps += arm_segment_length / step_increment[segment];
        if (dir) pos -= arm_segment_length; else pos += arm_segment_length;
        segment++;
    }

    // Calculate last incomplete segment steps
    if (fabsf(abs_destination - pos) > 0) steps += fabsf(abs_destination - pos) / step_increment[last_segment];

    return steps;
}
#endif

void Settings::convert_rotary_steps_to_degrees(float *position, const int32_t *steps, uint8_t n_axis) const {
    for (uint8_t idx = 0; idx < n_axis; idx++) position[idx] = (float) steps[idx] / steps_per_degree;
}

void Settings::convert_linear_steps_to_mm(float *position, const int32_t *steps, uint8_t n_axis) const {
    for (uint8_t idx = 0; idx < n_axis; idx++)
#ifdef ROCKER_HEAD
    position[idx] = get_rocker_axis_position(steps[idx]);
#else
    position[idx] = (float) steps[idx] / (float) steps_per_mm;
#endif
}

float Settings::convert_linear_steps_to_mm(const int32_t steps) const {
#ifdef ROCKER_HEAD
    return get_rocker_axis_position(steps);
#else
    return (float) steps / (float) steps_per_mm;
#endif
}
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

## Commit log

2023-03-04 Board fixes
    [stepper_drivers.kicad_sch, stm32-head.kicad_pcb, stm32-head.kicad_sch]
2023-03-05 HW fixes
    [stepper_drivers.kicad_sch, stm32-head.kicad_pcb, stm32-head.kicad_sch]
2023-03-08 Address LED light support.
2023-03-11 Some tweaks
    [stepper_drivers.kicad_sch, stm32-head.kicad_pcb, stm32-head.kicad_sch]
2023-03-11 Disable steppers on movement end when in zero position.
2023-04-02 PCB v0.3 went to production
    [stm32-head.kicad_pcb, stm32-head.kicad_sch]
2023-04-10 - RS-485 timing fix - vacuum sensor read command
    [control.cpp, control.h, stepper.cpp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]

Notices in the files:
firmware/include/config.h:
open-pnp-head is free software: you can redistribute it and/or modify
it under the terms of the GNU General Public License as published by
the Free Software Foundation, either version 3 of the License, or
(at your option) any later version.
